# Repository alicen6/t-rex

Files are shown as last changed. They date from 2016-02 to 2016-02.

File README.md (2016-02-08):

# T-Rex

This is the next step in my "Wooden Menagerie" project. I decided to make a t-rex in the same general style as the animals that I had previously made. This was also an experiment to see how patterns in laser cut wood would flex as a pivot to mimic body motions.

## Files

There are two folders of files, one has the original solidworks files, the other has the DXF files for cutting with a laser.

The solidworks model allows you to adjust, recreate, change and do whatever you would like to the overall t-rex design and model. You can also easily move the model around in a 3D environment in order to see what parts go where when building the t-rex.

The DXF files are what you will use to cut out all of the pieces. DXF files are flat files that give the laser a path to follow for cutting parts. There are also nested files with all the parts already laid out. There is a file for a laser that can accommodate 24" x 36" material. In order to cut all the parts out on a laser that can handle 20" x 32", there are two separate files to cut. I have provided three different types of files, Illustrator, PDF, and DXF. All are the same and should provide the same outcome.

The one excel file is for the number of parts needed of each different shape. Some of the parts are needed twice, four times, some 16+. Using this file when laying out all the parts for nesting is very helpful.

## Materials

This t-rex was designed with 1/8" material in mind, that could be wood, plastic, or anything really as long as it can be cut properly and is the right thickness.

The holes are all designed to fit 3/16" dowels.

Ideally, I'd love to see this made with bright green, clear plastic and metal rods for all the pivots.

## Process

The same as the previous creatures, when constructing this dinosaur, I would suggest dry fitting parts and pivot shafts before using some kind of adhesive to finalize the position. I suggest using super glue or fast dry epoxy.

The first step is to cut all your parts out with a laser or router. Once you have your pieces, start to assemble, using dry fits to determine how long each pivot rod needs to be for each area.

When gluing together pivots, be careful not to glue faces together that should still slide, this will ruin your pivot and make a messy model.

## Changes

There might be changes made to the model in the future to fix problems and enhance the movement.

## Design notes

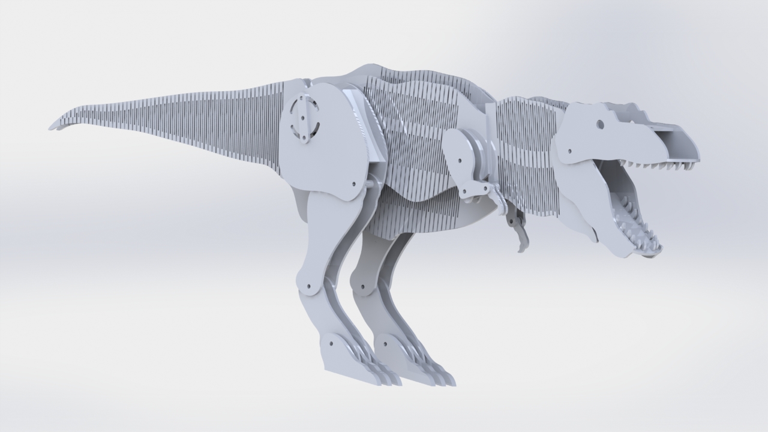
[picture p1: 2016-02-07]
trex.JPG

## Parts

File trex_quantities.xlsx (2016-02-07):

Part Name | Quantity
ankle | 4
body center | 1
body sides | 2
bottom jaw profile | 2
bottom jaw spacer | 1
calf brace | 2
calf | 4
forward neck flex support | 1
head back bridge | 1
head profile | 2
hip brace left | 1
hip brace right | 1
hip joint bearing cap | 6
lower arm | 4
neck ivit base brace | 1
neck rotate bearing cap | 2
nody neck bearing | 1
nose bridge | 1
shoulder brace left | 1
shoulder brace right | 1
tail center | 2
thigh brace | 2
thigh | 4
throat side flex | 2
toes | 12
tooth | 34
top jaw spacer | 1
upper arm | 4
wrist spacer | 36
wrist | 4

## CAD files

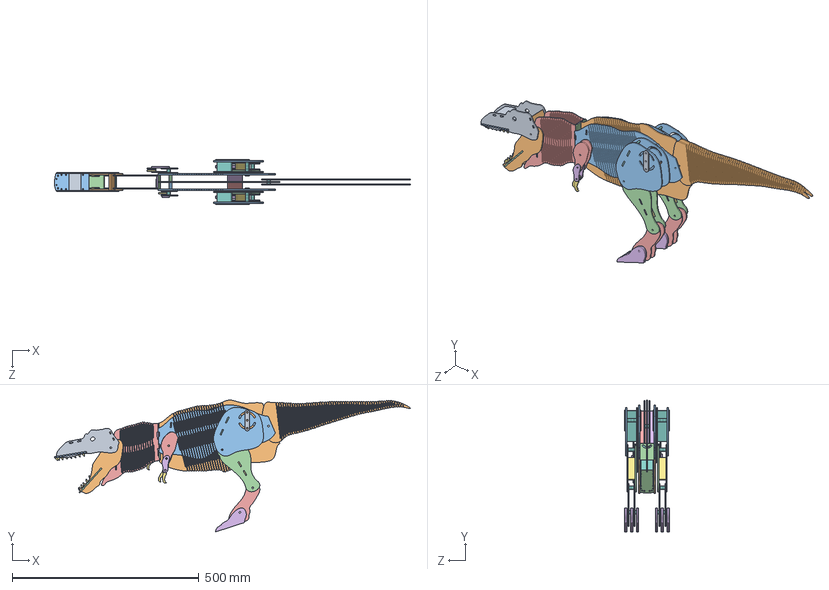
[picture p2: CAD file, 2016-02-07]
solidworks_files/rex.SLDASM
952.2 x 352.8 x 120.7 mm
head profile x 2
bottom jaw profile x 2
top jaw spacer
bottom jaw spacer
throat side flex x 2
neck ivit base brace
tooth x 34
forward neck flex support
neck rotate bearing cap
body center
body sides x 2
nody neck bearing
upper arm x 4
lower arm x 4
wrist x 4
wrist spacer x 54
nose bridge
head back bridge
thigh x 4
calf x 4
ankle x 4
toes x 12
calf brace x 2
thigh brace x 2
hip joint bearing cap x 6
tail center x 2
shoulder brace left
shoulder brace right
hip brace left
hip brace right

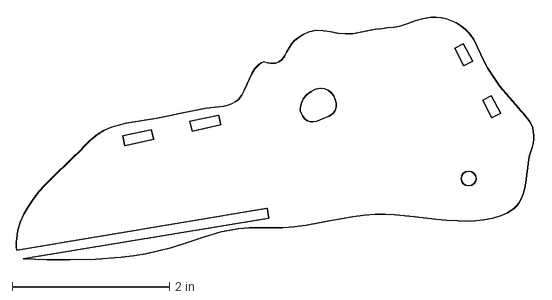
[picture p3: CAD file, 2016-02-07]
dxf_files/head profile.DXF
6.60 x 3.10 in

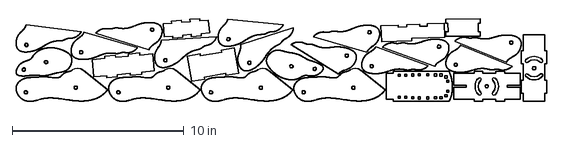
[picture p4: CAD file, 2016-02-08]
dxf_files/nested_files/32x20 Sheet 2.dxf
30.9 x 4.82 in

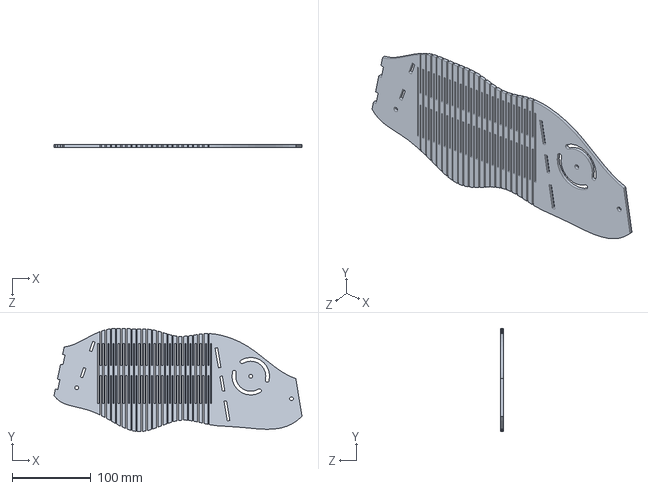
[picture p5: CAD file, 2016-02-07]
solidworks_files/body sides.SLDPRT
314.3 x 130.9 x 3.17 mm

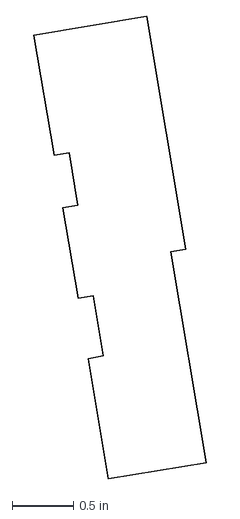
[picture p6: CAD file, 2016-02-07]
dxf_files/hip brace left.DXF
1.41 x 3.79 in

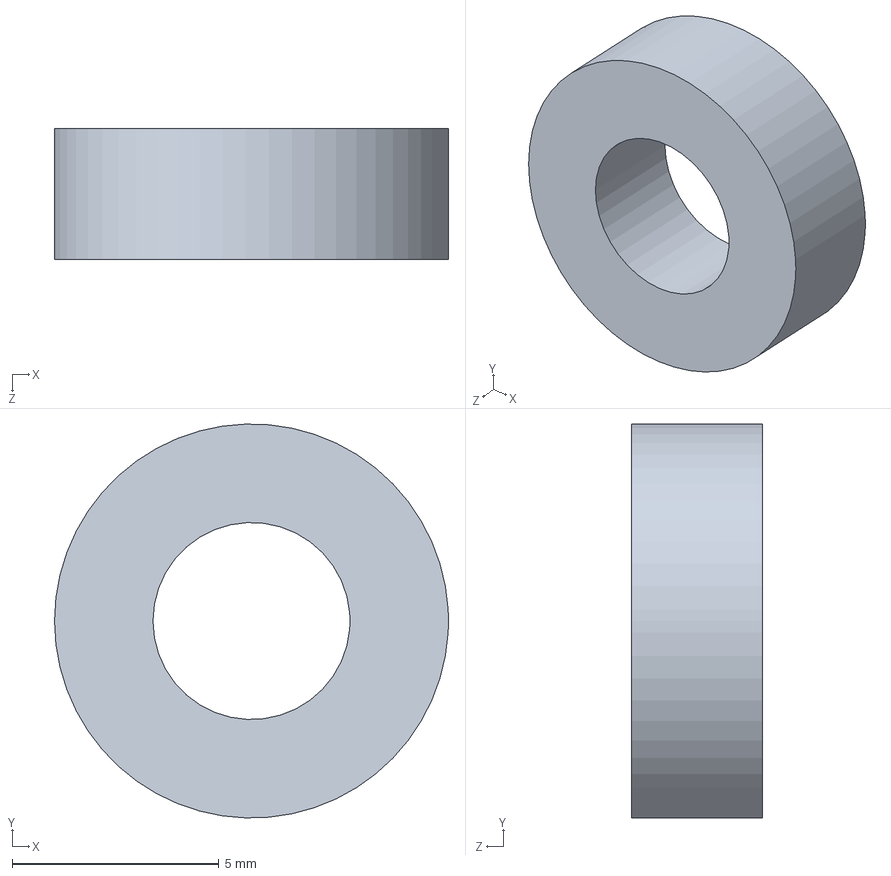
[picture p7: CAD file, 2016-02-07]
solidworks_files/wrist spacer.SLDPRT
9.53 x 9.52 x 3.17 mm

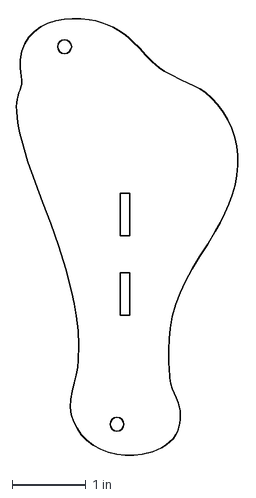
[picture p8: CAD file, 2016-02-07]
dxf_files/calf.DXF
3.02 x 5.98 in

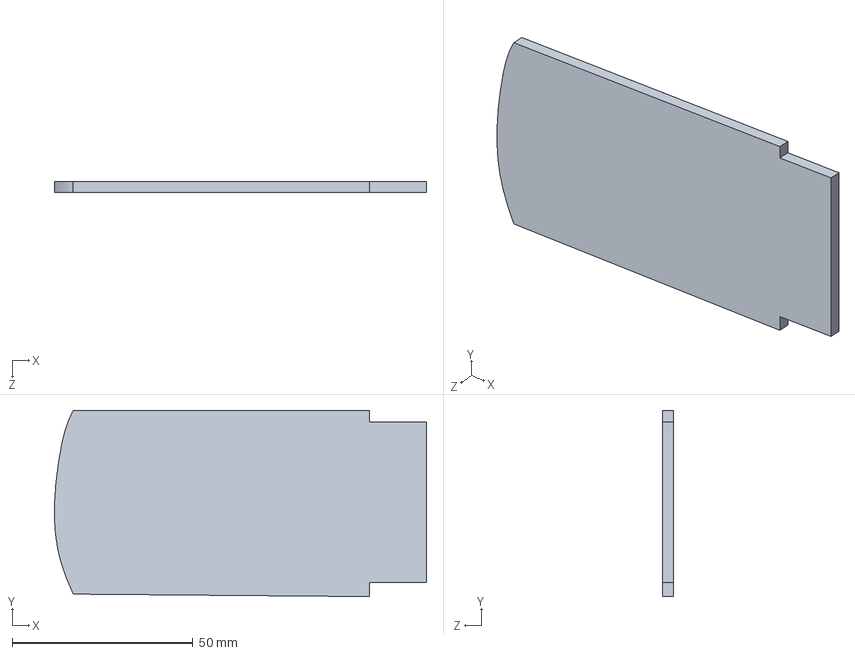
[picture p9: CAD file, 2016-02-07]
solidworks_files/top jaw spacer.SLDPRT
102.9 x 51.5 x 3.17 mm

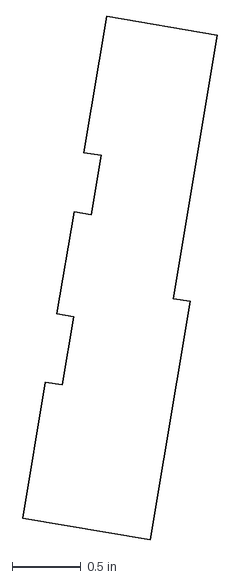
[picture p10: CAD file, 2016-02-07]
dxf_files/hip brace right.DXF
1.41 x 3.79 in

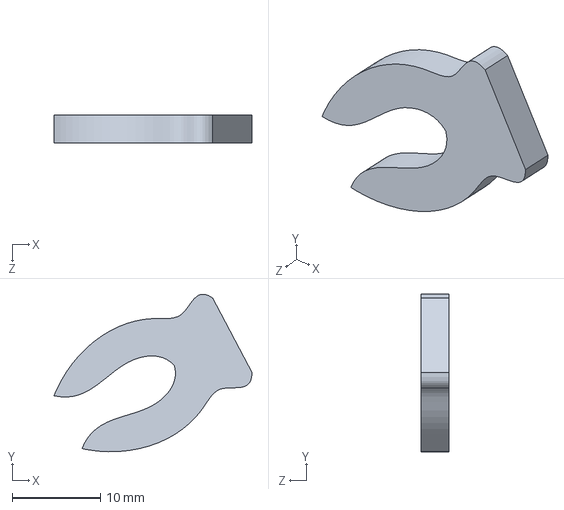
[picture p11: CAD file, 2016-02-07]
solidworks_files/claw.SLDPRT
22.4 x 17.9 x 3.17 mm

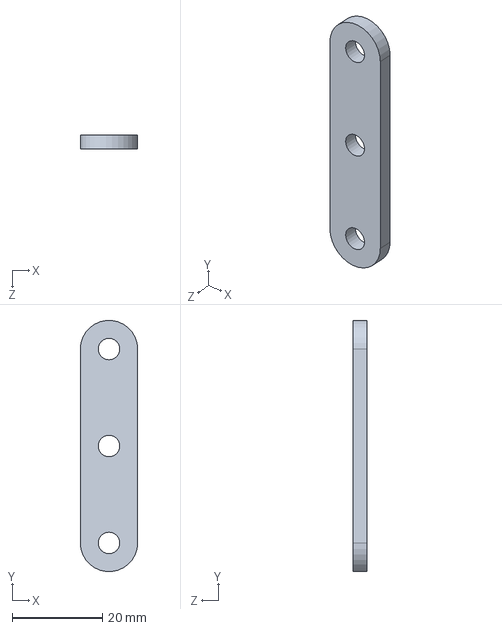
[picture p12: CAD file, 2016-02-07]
solidworks_files/hip joint bearing cap.SLDPRT
12.7 x 55.5 x 3.17 mm

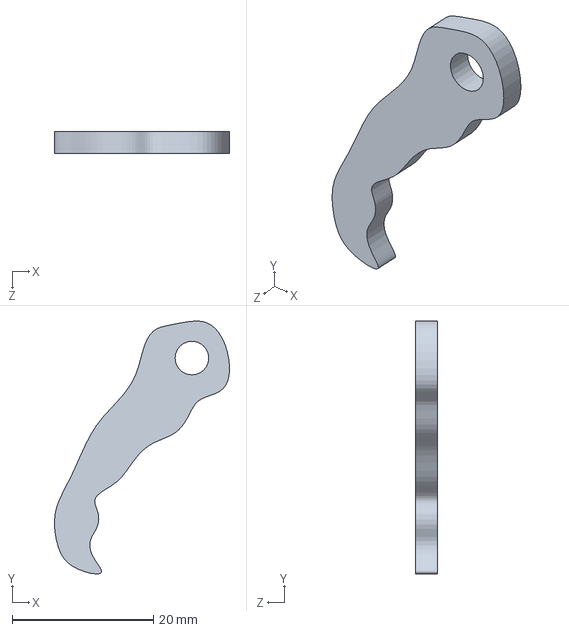
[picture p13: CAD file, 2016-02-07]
solidworks_files/wrist.SLDPRT
24.8 x 35.8 x 3.17 mm

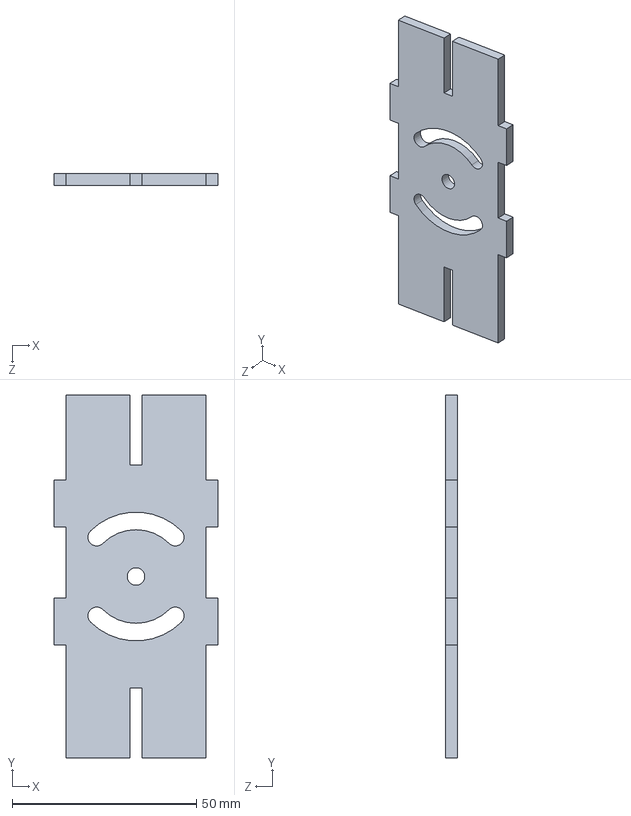
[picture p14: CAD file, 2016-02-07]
solidworks_files/nody neck bearing.SLDPRT
44.4 x 98.5 x 3.17 mm

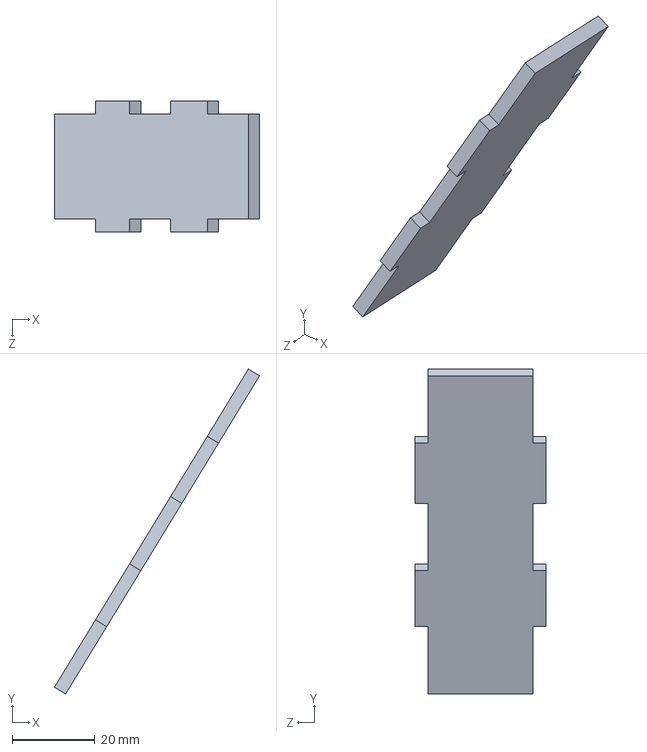
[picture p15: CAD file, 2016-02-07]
solidworks_files/thigh brace.SLDPRT
49.6 x 78.6 x 31.8 mm

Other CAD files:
solidworks_files/neck ivit base brace.SLDPRT
solidworks_files/bottom jaw spacer.SLDPRT
solidworks_files/head back bridge.SLDPRT
solidworks_files/bottom jaw profile.SLDPRT
dxf_files/ankle.DXF
dxf_files/body center.DXF
dxf_files/body sides.DXF
dxf_files/bottom jaw profile.DXF
dxf_files/bottom jaw spacer.DXF
dxf_files/calf brace.DXF
dxf_files/forward neck flex support.DXF
dxf_files/head back bridge.DXF
dxf_files/hip joint bearing cap.DXF
dxf_files/lower arm.DXF
dxf_files/neck ivit base brace.DXF
dxf_files/neck rotate bearing cap.DXF
dxf_files/nody neck bearing.DXF
dxf_files/nose bridge.DXF
dxf_files/shoulder brace left.DXF
dxf_files/shoulder brace right.DXF
dxf_files/tail center.DXF
dxf_files/thigh brace.DXF
dxf_files/thigh.DXF
dxf_files/throat side flex.DXF
dxf_files/toes.DXF
dxf_files/tooth.DXF
dxf_files/top jaw spacer.DXF
dxf_files/upper arm.DXF
dxf_files/wrist spacer.DXF
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

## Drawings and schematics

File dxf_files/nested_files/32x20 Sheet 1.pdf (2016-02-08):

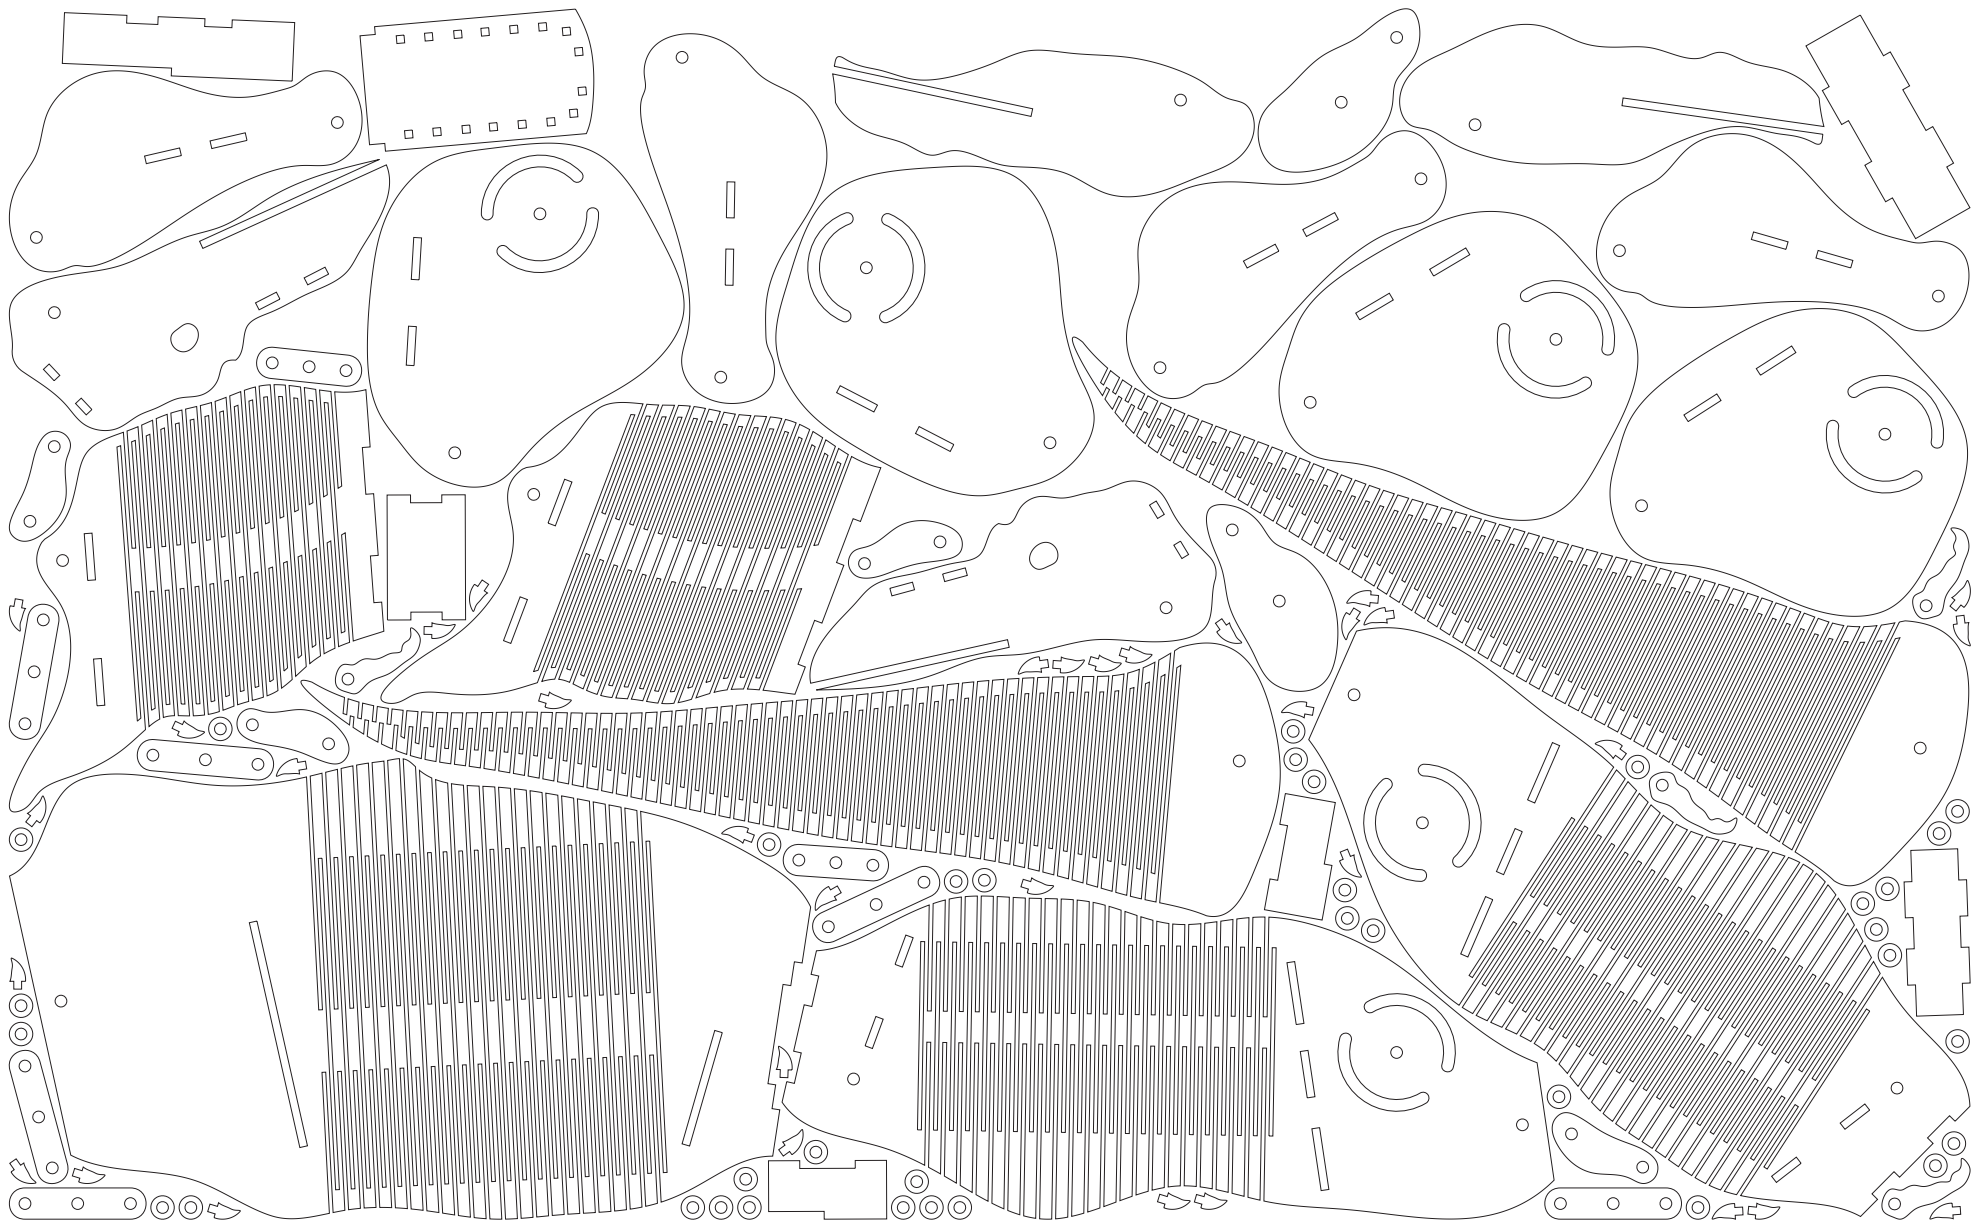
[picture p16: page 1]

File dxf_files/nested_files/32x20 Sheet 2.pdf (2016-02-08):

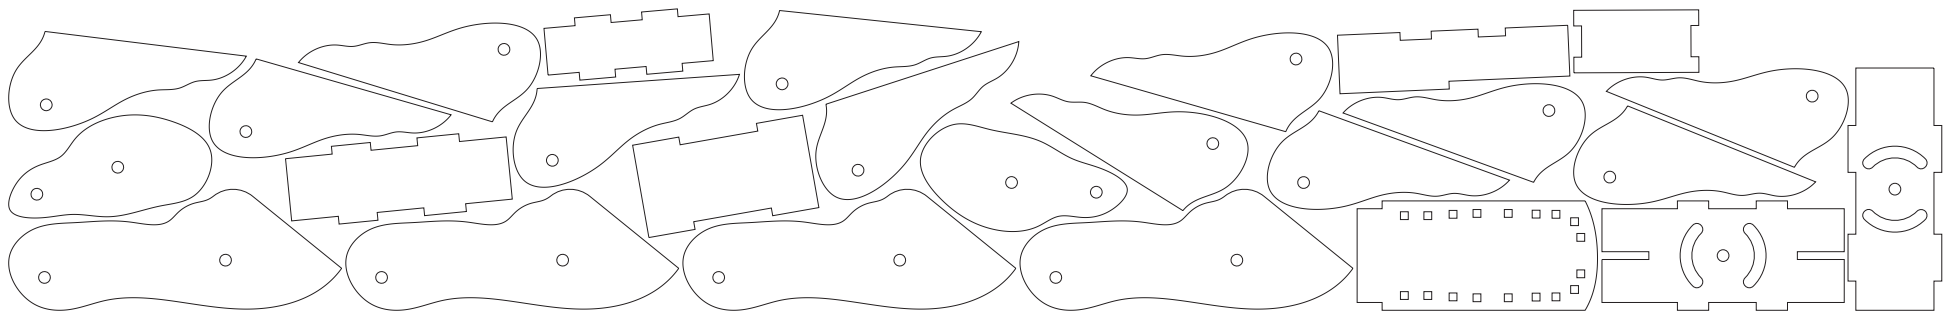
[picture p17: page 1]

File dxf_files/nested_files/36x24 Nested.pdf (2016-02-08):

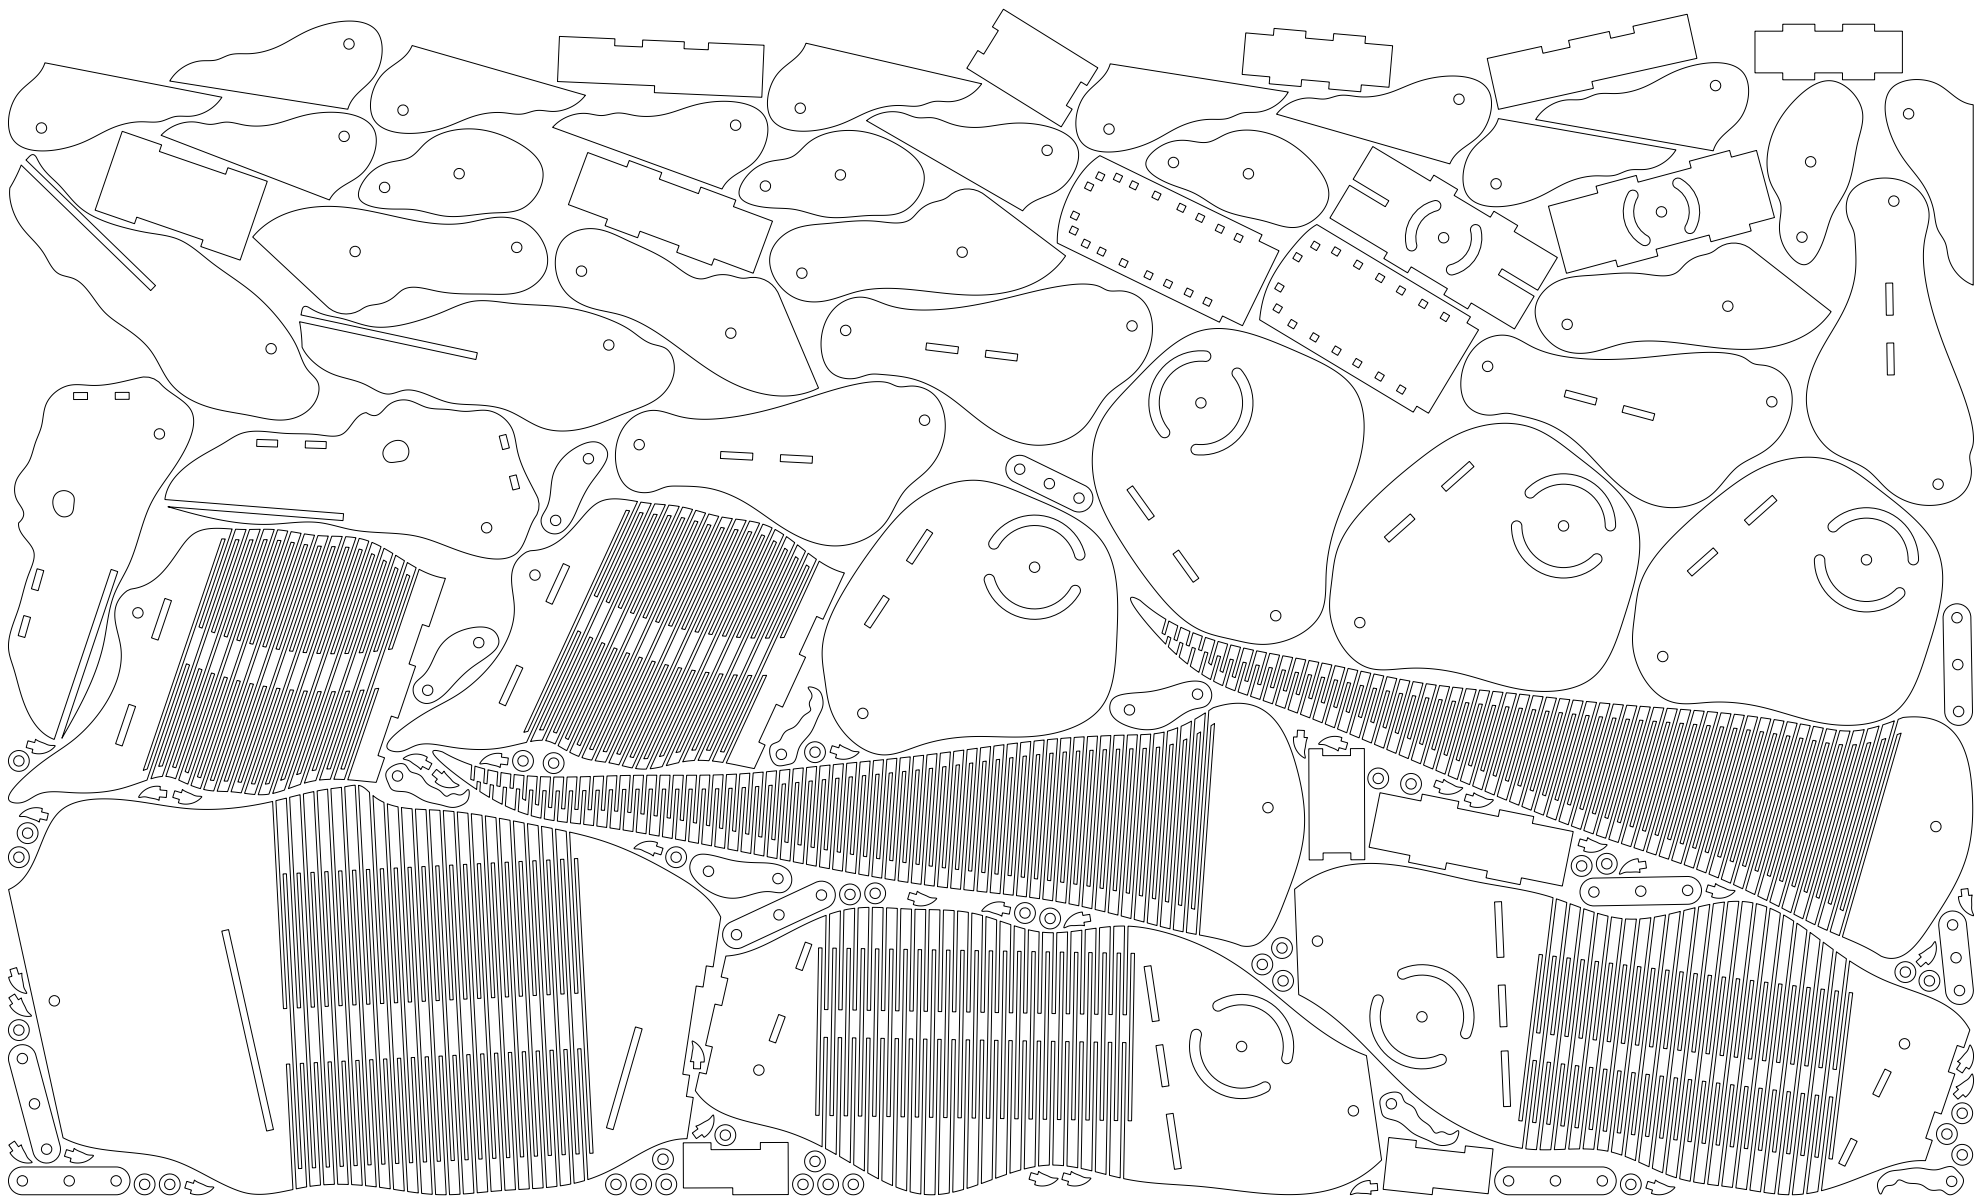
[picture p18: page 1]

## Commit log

2016-02-07 add DXF files and excel quantities
    [ankle.DXF, body center.DXF, body sides.DXF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]
2016-02-08 added nested files
    [32x20 Sheet 2.dxf]
